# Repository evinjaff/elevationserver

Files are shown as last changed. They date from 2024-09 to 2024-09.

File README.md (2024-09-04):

# elevationserver - Remotely Controlling a Standing Desk via Optocouplers on a Pi

Raspberry Pi circuit Final mount and wiring

# Backgroud

I was tasked with trying to reverse engineer the serial port on a standing desk so that we could manipulate it remotely on a raspberry pi for automated testing of a system. I did some probing of the serial connection, and even got to finally use my [Raspberry Pi debug probe](https://www.raspberrypi.com/products/debug-probe/) to try and read UART signals. While I did fetch some bytes, a replay attack failed to get the table manipulated over serial. Because this table has easily usable buttons, I decided instead to wire up optocouplers to press the buttons with a raspberry pi.

# The Server

The actual server that drives the table up and down is pretty simple. It just uses Flask and has one endpoint that you supply the percentage up or down you want the table to be positioned in addition to a root endpoint that tells you if the server is running. 

The way it manipulates the table is that I've set the 4 presets to be at 0, 33, 66, and 100 percent of the full height. Based on the value of the number, the Pi clicks a preset and then moves the table up or down to get as close to the specific percentage as possible. 0, 33, 66, and 100 are guaranteed to be stable amounts since they're presets while the other ones are closer to guesswork.

The OpenAPI spec in YAML form is [here](openapi.yaml) with HTML client docs [here](openapi-docs.html).

# How To Build this

## Prep the display for soldering

This table has a display unit with buttons that is connected to a controller unit via an RJ45 jack. Disconnect the RJ45 plug from the display unit and then unscrew the display unit from the table using a Philips head screwdriver. Then, remove the board it from the plastic shell using a Phillips head screwdriver to remove the 4 screws in the rear of the unit. Then remove the tape holding the metal circles where the buttons are to expose the pads that are bridged to trigger the buttons. With the board ready, we can now solder.

### Soldering

Using a soldering iron, we solder two wires to each button. While you could easily strip one end of a Dupont wire to get a connection from the board, I find these wires very difficult to solder to pads because the wires are very thin (often 28 AWG). That's why I reccomend using thicker non-terminated wire with an AWG closer to 22 AWG. As always with unleaded solder, remember to be liberal with your flux and use a helping hands to help hold the board in place. Also, test your solder joints for [continuity with a multimeter](https://www.wikihow.com/Test-Continuity-with-a-Multimeter)- you don't want any globs of solder shorting out buttons.

Once you've confirmed it all works, I'd recommend throwing some Kapton tape over the joints to protect them from shorting.

### Terminating with a Dupont Connector

I'm embarrased to say that I spent probably 1-2 hours terminating these wires because it took me a while to figure out how to get them to slip through the black dupont sleeve. I'm not going to try and explain it here, I'll just point you to a [youtube video that might explain it better](https://www.youtube.com/watch?v=jET1QTP1B7c
). Since these go on a breadboard, I'd reccomend terminating with male ends. Plus, if you can't get the sleeve on the metal, you can still just stick the pin in the breadboard.

### Optocoupler circuit

Optocouplers are great pieces of techology. They comprise of an LED and a phototransistor. On the control side of the optocoupler (in our case the raspberry pi), the controller is connected to an LED that it can turn on and off. On the other side of the optocoupler chip, the phototransistor connects the two pins if the LED is on, thereby isolating the two circuits, preventing any need for nasty buck converters or diodes to manipulate the other system. 

When wiring up our optocouplers (in our case a SHARP PC817), this is what you want the circuit to theoretically look like:

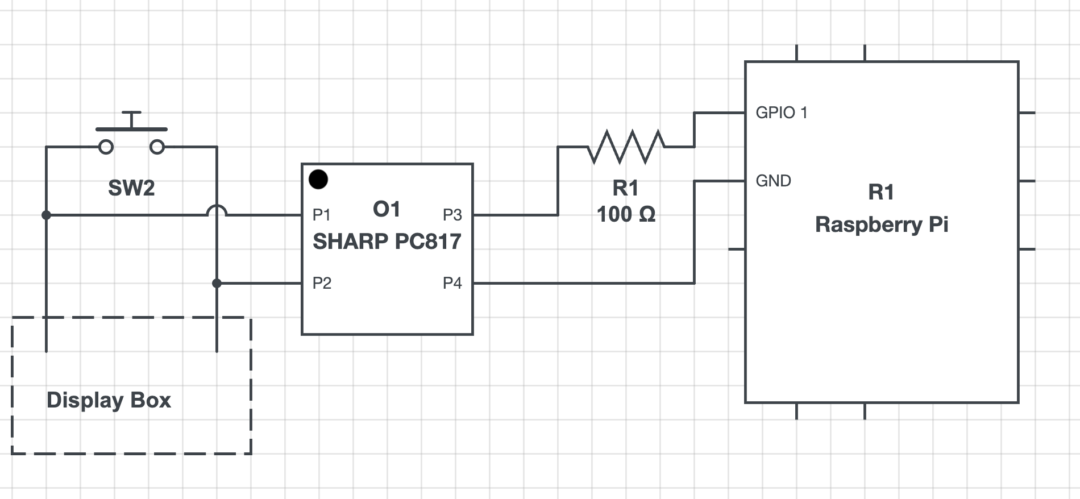
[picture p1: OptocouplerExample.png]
Optocoupler circuit Example circuit diagram indicating how to wire GPIO pins to a SHARP PC817 optocoupler


We need a resistor to drop the voltage so we don't burn out the LED, and we want the Pi to be entirely hooked up to the right legs of the optocoupler (the "control side") while the left legs connect the leads of the buttons to each side of the optocoupler to close the switch.

The optocouplers from gikfun off Amazon seemed to have various levels of wear, and even an in-spec resistor sometimes failed to trigger the phototransistor, requiring me to wire my resistors in parallel to drop the resistance. If it's not working, double check the wiring and then play around with different resistances.

### Connecting to a Pi and configuring your GPIO pins

To test the GPIO pins, I'd reccomend using the testPin.py file. But that can be a little annoying so if you want something even simpler, use this little script. My script uses the Broadcom mappings, so use the "GPIO X" number from https://pinout.xyz/ to figure out which one works.

```py 

import RPi.GPIO as GPIO
import time
 
pin = 21         # The pin connected to the LED
interval = .25   # The length of time to blink on or off

# Setting to BCM will use Broadcom's GPIO numbers, while using Pi will set it to the pi's physical pin count
GPIO.setmode(GPIO.BCM)
GPIO.setwarnings(False)
GPIO.setup(pin, GPIO.OUT)

# write to pin
GPIO.output(pin, GPIO.HIGH)
time.sleep(interval)
GPIO.output(pin, GPIO.LOW)

```

Then, you can fill in the correct pin mappings in `Config.py` that match how you wired it up:

```py
GPIO_LOOKUP = {
    "preset1": 17, # sets at 72
    "preset2": 6, # sets at 88
    "preset3": 13, # sets at 104
    "preset4": 5, # sets at 120
    "up": 26,
    "down": 27,
}
```

### Run the server

Since this is likely running on your own network, I'd reccomend adding a DHCP entry that points to the Raspberry Pi's IP. 

Bonus points for running the server as a systemd daemon too, that way you don't even need to SSH in when you reboot the pi. You can do this using the same tutorial from my [Oatmeal Computer Vision Server](https://github.com/evinjaff/oatmeal-cv-server?tab=readme-ov-file#run-it-as-a-systemd-service):

`elevationserver.service`
```toml
[Unit]
Description=Elevation Server
After=multi-user.target

[Service]
Type=idle
ExecStart=/path_to_this_repo/pi/venv/bin/python /path_to_this_repo/ElevationServer.py
StandardOutput=journal
StandardError=journal

[Install]
WantedBy=multi-user.target
```

Enable the service by typing `systemctl enable elevationserver.service`

Start the service by typing `systemctl start elevationserver.service`

Check that it worked by typing `systemctl status elevationserver.service`

## Mounting

Once you're sure that this works, you can mount it all up. I remixed a common raspberry pi mounting plate to include a tray to hold the display unit in addition to the breadboard. Should print ok with no supports needed. Here's a render of the 3D model, it's a little tight to put in the breadboard, but it will fit snugly.

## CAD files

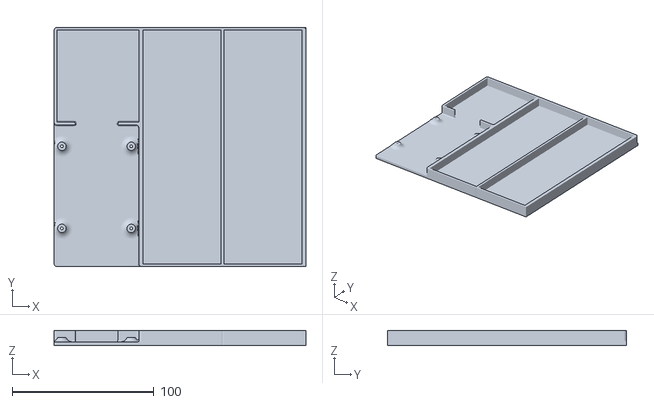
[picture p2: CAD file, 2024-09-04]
mount.stl
178.1 x 169.0 x 10.5

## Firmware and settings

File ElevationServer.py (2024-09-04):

from flask import Flask, request, jsonify
from Config import GPIO_LOOKUP
from GPIOTest import testPin, initializeGPIO
import time

app = Flask(__name__)

# global variable
current_level = 0

# Constants
# How long to fire the optocouplers to press a preset
MEMORY_BUTTON_PRESS_DURATION = 0.125
# The ratio of seconds / number of ticks moved
TICKS_PER_SECOND_CONSTANT = 1 / 4
# factor of how much to fudge timing to prevent input while a preset is moving
FUDGE_FACTOR = 1.5


# HTTP Code
# Quick Wakeup test to make sure the server is running
@app.route("/")
def hello_world():
    return "Elevation Server is running!"

@app.route("/setElevation", methods=["GET"])
def setElevation():
    global current_level
    percentage = request.args.get('percentage', type=int)
    
    if percentage is None:
        return jsonify({"error": "No percentage value provided"}), 400
    
    if percentage >= 0 and percentage <= 100:
        setNonElevation(percentage=percentage, previous_level=0)
    else:
        return jsonify({"error": "Invalid percentage value"}), 400

    current_level = percentage
    return jsonify({}), 200



## Routines that manipulate GPIO for routing

# TODO: fill in the GPIO pins
def elevationPreset(mode, previous_level=0):
    '''
    Fires the optocoupler (range 1-4) which selects a preset elevation.

    Parameters:
    mode (int): The preset elevation to select. Range 1-4 where 1 is 0%, 2 is 33%, 3 is 66%, 4 is 100%

    Returns:
    The elevation level set
    '''

    if mode < 1 or mode > 4:
        raise ValueError(f"Invalid mode {mode}. Must be between 1 and 4.")
    
    # Fire the optocoupler

    modestring = "preset" + str(mode)

    if modestring in GPIO_LOOKUP:
        testPin(modestring, duration=MEMORY_BUTTON_PRESS_DURATION, interactive=False)
    else:
        raise LookupError(f"Couldn't find modestring: {modestring} in {GPIO_LOOKUP}")


def setNonElevation(percentage, previous_level=0):
    '''
    Fires the up and down signals to approximate a percentage but there will likely be some error
    
    Parameters:
    percentage (int): The percentage to raise the table to
    previous_level (int): The previous level to move to. If set to None, will set the table to 0 and raise

    Returns:
    The elevation level set
    '''
    global current_level
    presets = [0, 33, 66, 100]

    if percentage in presets:
        return elevationPreset( (percentage // 33) + 1 )

    # Define the preset values
    # Find the closest preset value
    closest_preset = min(presets, key=lambda x: abs(x - percentage))
    difference_from_previous = abs(current_level - closest_preset)
    # convert to mode index
    closest_preset = (closest_preset // 33) + 1

    print(f"Setting preset to {closest_preset}")
    elevationPreset(closest_preset)

    
    # add sleep time to elevation Preset
    time.sleep(difference_from_previous * TICKS_PER_SECOND_CONSTANT * FUDGE_FACTOR)
    
    # Calculate the difference between the target and the closest preset
    difference = percentage - closest_preset
    # Use goUp or goDown to reach the target value
    duration = abs(difference) * TICKS_PER_SECOND_CONSTANT

    print(f"{difference} runs for {duration} seconds")

    if difference > 0:
        testPin("up", duration=duration, interactive=False)
    elif difference < 0:
        testPin("down", duration=duration, interactive=False)


    return percentage


# startup the server
if __name__ == '__main__':

    initializeGPIO()
    app.run(debug=True, port=8080, host='0.0.0.0')

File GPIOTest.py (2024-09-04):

#import the GPIO and time package
import RPi.GPIO as GPIO
import time
import Config


TEST_INTERVAL_PAUSE = 10

def initializeGPIO():
    GPIO.setmode(GPIO.BCM)

    for i in Config.GPIO_LOOKUP:
        print(f"Setting pin {Config.GPIO_LOOKUP[i]} (purpose: {i}) as OUT")
        GPIO.setup(Config.GPIO_LOOKUP[i], GPIO.OUT)
        print(i)

def testPin(GPIO_ID , duration=3, interactive=False):

    print(f"Setting pin {Config.GPIO_LOOKUP[GPIO_ID]} (purpose: {GPIO_ID}) as OUT")
    GPIO.setup(Config.GPIO_LOOKUP[GPIO_ID], GPIO.OUT)

    print(f"Poking {GPIO_ID} on pin {Config.GPIO_LOOKUP[GPIO_ID]}")
    GPIO.output( Config.GPIO_LOOKUP[GPIO_ID] ,True)
    time.sleep(duration)
    GPIO.output( Config.GPIO_LOOKUP[GPIO_ID],False)
    time.sleep(duration)

    if interactive:
        input(f"Did {GPIO_ID} work? (y/n): ")



def testSuite(duration=3):

    initializeGPIO()
    
    for i in Config.GPIO_LOOKUP:
        testPin(i, duration=duration, interactive=True)
    GPIO.cleanup()




def main():
    print("type \"all\" to test all or type a number below to test a specific one: ")

    Select = {
        "preset1": 1,
        "preset2": 2,
        "preset3": 3,
        "preset4": 4,
        "up": 5,
        "down": 6,
    }

    print(Select)

    response = input("#")

    if "all" in response:
        testSuite()
        return
    
    for i in Select:

        GPIO.setmode(GPIO.BCM)
        if str(Select[i]) in response:
            testPin(i, duration=2, interactive=True)


if __name__ == "__main__":
    main()

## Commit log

2024-08-30 update to be pin-based
2024-09-03 Pins fixed and flask server endpoint added
    [ElevationServer.py]
2024-09-04 fix bug in converting preset
    [ElevationServer.py]
2024-09-04 Add photos and update readme with fudge
    [mount.stl, mount_ascii.stl]
2024-09-04 fix ascii stl
    [mount_ascii.stl]
